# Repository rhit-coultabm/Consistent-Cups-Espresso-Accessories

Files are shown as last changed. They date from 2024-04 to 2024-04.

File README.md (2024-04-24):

# Consistent-Cups-Espresso-Accessories
Open Source DIY solution to create Bluetooth-compatible pressure sensor and scale to use with a manual espresso machine. 

## Table of Contents
- [Consistent-Cups-Espresso-Accessories](#consistent-cups-espresso-accessories)
   - [Table of Contents](#table-of-contents)
   - [Project Background and Introduction](#project-background-and-introduction)
      - [Semi-Automatic Espresso Machines](#semi-automatic-espresso-machines)
      - [Manual Espresso Machines](#manual-espresso-machines)
   - [Description of Solution](#description-of-the-solution)
      - [Bill of Materials](#bill-of-materials)
   - [Pressure Sensor](#pressure-sensor)
      - [Components Used](#components-used)
      - [Casing Files](#casing-files)
      - [Assembly Instructions](#assembly-instructions)
   - [Scale](#scale)
      - [Components Used](#components-used-1)
      - [Casing and PCB Files](#casing-and-pcb-files)
      - [Assembly Instructions](#assembly-instructions-1)
   - [Flashing the Devices](#flashing-the-devices)
   - [Connecting with Profiler Apps](#connecting-with-profiler-apps)

## Project Background and Introduction

The market for espresso machines is a vastly large and competitive one. Every individual has their own preferences and lifestyles which result in the need for different machines. There are so many methods for making espresso that vary significantly in user effort, time, and price. 

### Semi-Automatic Espresso Machines

Automatic machines require little user effort and time to extract an espresso shot. However, the large downside to these machines is that, generally speaking, they cost upwards of $300-400 depending on the additional features and components they have. Once the grinds are tamped in the portafilter, the machine automatically applies the pressure for the duration of time that can sometimes be specified by the user.  

images

Figure 1: Semi-Automatic Espresso Machine Example 

### Manual Espresso Machines

Manual espresso machines require a significant amount of preparation, time, and effort. These machines are generally cheaper than their automatic counterparts, being found for upwards of $100. For these machines, once the grinds are tamped in the portafilter, the user must also heat their water to the desired temperature. The user then needs a scale underneath the cup to be able to see how fast they are extracting the espresso. After pulling the lever and applying pressure for a set amount of time, the extraction is finally complete. The downsides to this machine are the extensive clean-up time and the loss of water temperature during the extraction. However, this machine allows the user to have complete control over the amount of pressure and time variables for making their own ideal cup of espresso, perfect for connoisseurs. With the pressure transducer and scale, it would be even easier to repeat their results or tweak them to their preferences. An example of what this type of machine looks like is in the right image of Figure 3. 

Besides the bean and how it's roasted, a good cup of lever espresso relies on three main factors: Pressure, temperature, and speed of the pull.  The speed of pull is determined by the grind size of the bean and the pressure.  Pressure is controlled by pulling the machine's handle.  A monitor system lets you track and save the pressure and pull speed data to a template.  You can then follow the template when doing a future pull, enabling consistent tasting espresso. 

The downside to such systems is the cost.  An entry-level scale like the Acaia Lunar Espresso Scale is $250, and the pressure gauge is $460 from naked-portafilter (both pictured below). 

Capture

Figure 2: Naked Portafilter Smart Espresso Profiler 

Capture1

Figure 3: Acaia Lunar Espresso Scale 

## Description of the solution

The market for espresso machines is a vastly large and competitive one. Every individual has their own preferences and lifestyles which result in the need for different machines, which vary significantly in user effort, time, and price.  Manual lever espresso machines offer an affordable entrance into brewing quality espresso at home.  A monitor system helps the novice get consistent pulls of espresso by tracking and logging variables like pressure and speed of pull. The existing market design for the pressure sensor is $400 and the scale is $200, a steep cost that ends up at the same price level as some higher-end automatic machines. This solution is an open-source pressure sensor and scale system that wirelessly connects to the SE Profiler or Coffee Flow phone app. This is all accomplishable with the materials posted below in the BOM, a soldering iron, a 3D printer, and a computer!

### Bill of Materials

[BOM.xlsx](https://github.com/rhit-coultabm/Consistent-Cups-Espresso-Accessories/files/15097891/BOM.xlsx)

## Pressure sensor

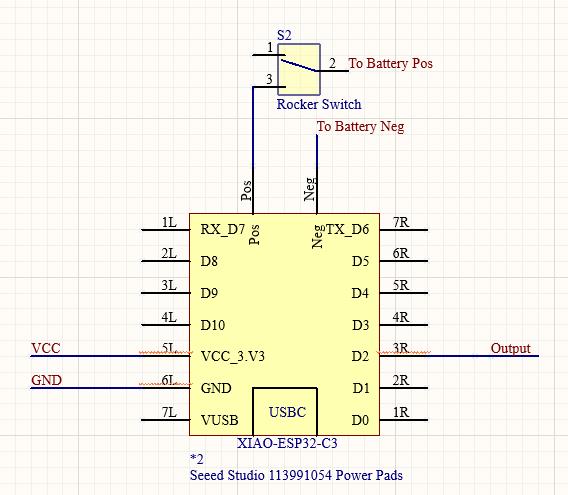
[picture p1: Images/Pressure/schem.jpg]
pressure sensor schematic


Figure 6: Wiring diagram

### Components used
   - Seeduino
   - Pressure Sensor
   - Battery
   - On/off switch
   - Casing
  
   Shown here:
  
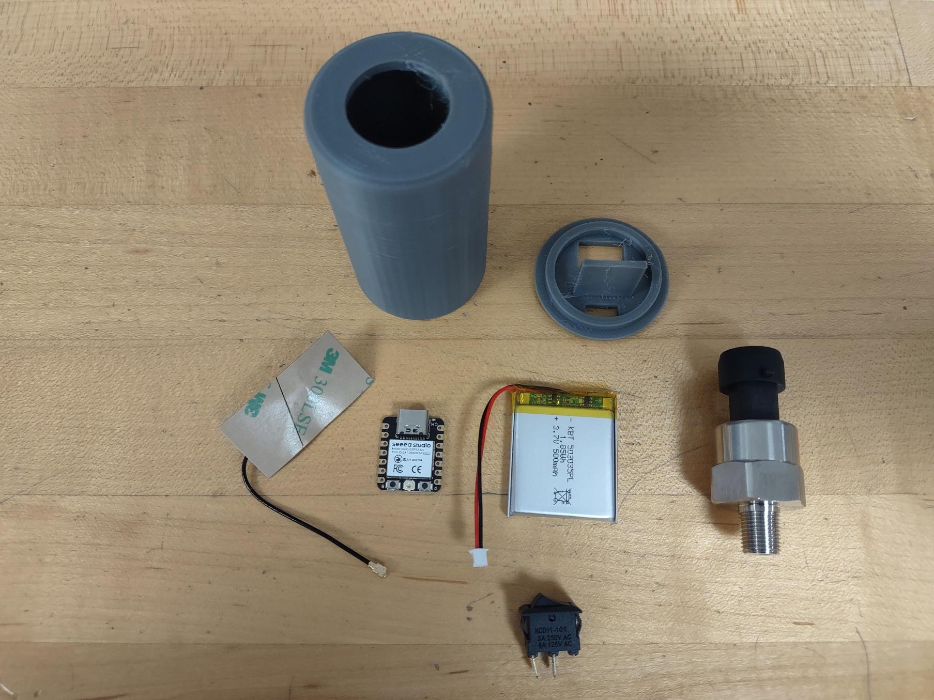
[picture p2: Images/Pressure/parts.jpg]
pressure sensor parts


### Casing files
   
[Body](Enclosure_Files/Pressure_Sensor/pressure_base.STL)

[Cap](Enclosure_Files/Pressure_Sensor/pressure_end.STL)

### Assembly Instructions

#### Step 1: Solder Power connections

- Using the battery, two short wires, and the seeduino (shown below in figure 4) follow the wiring diagram (shown above in figure 6) connecting the battery positive (red) wire to one of the pins on the switch. Then the battery negative (black) wire to the negative pin on the back of the seeduino. Next, solder a wire from the other switch pin to the positive pin on the back of the seeduino. 
- This final product attached to the casing cap is shown below in figure 5

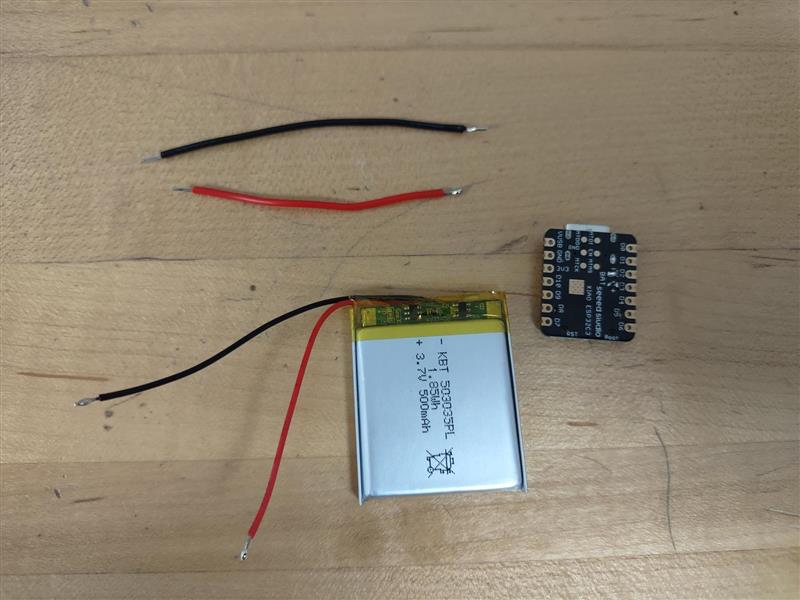
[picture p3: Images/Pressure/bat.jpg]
battery and xiao


Figure 4: Items needed

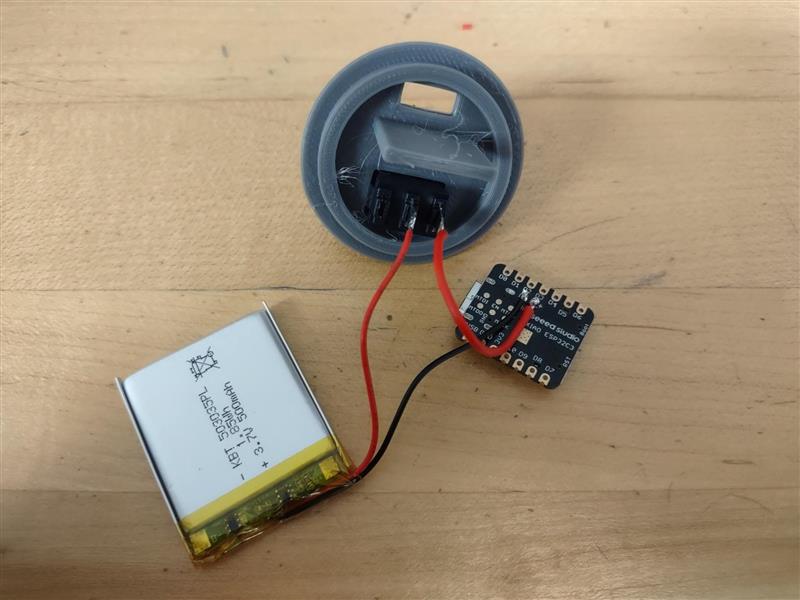
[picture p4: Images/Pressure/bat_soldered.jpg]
battery soldered with switch


Figure 5: final product of this step

#### Step 2: Solder Pressure Sensor

- Using the two figures below, wire the pressure sensor with the Vcc to pin Vcc, the ground to ground, and the output to pin D2
- Make sure that the pressure sensor is wired through the hole in the casing to the seeduino, this is to ensure that it can all be put together in the final step

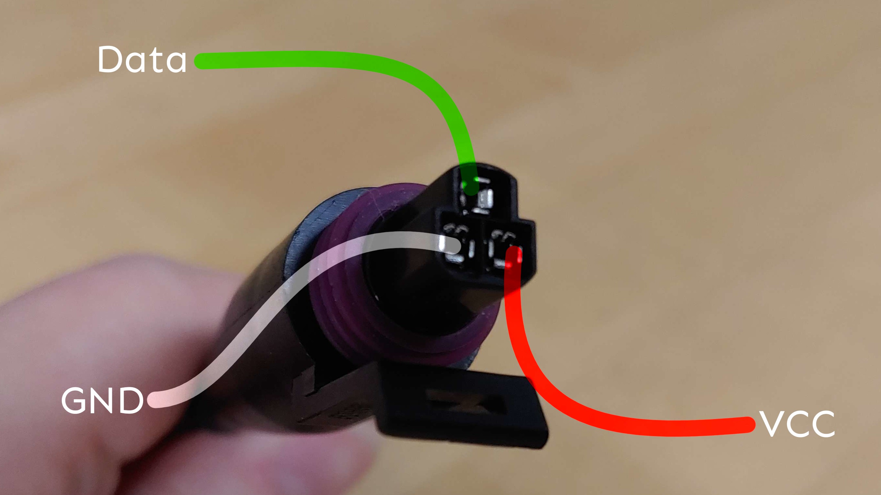
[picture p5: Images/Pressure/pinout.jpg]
sensor pinout


Figure 7: Sensor Wiring assignments

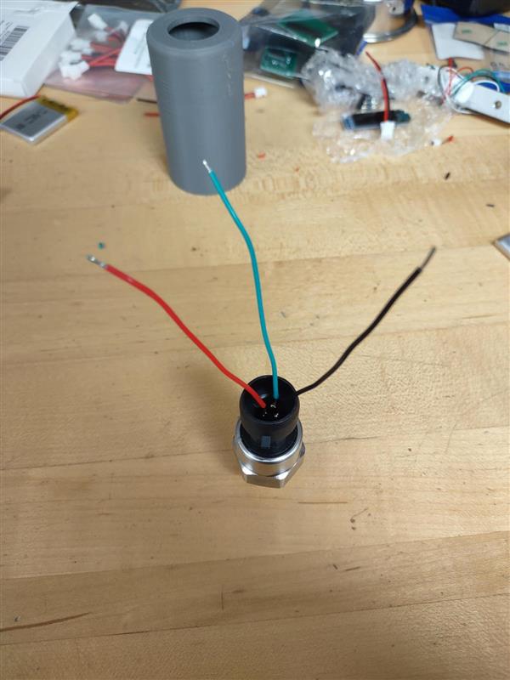
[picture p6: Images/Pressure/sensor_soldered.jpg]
sensor pins soldered


Figure 9: Wired pressure sensors with matching colors from figure 8

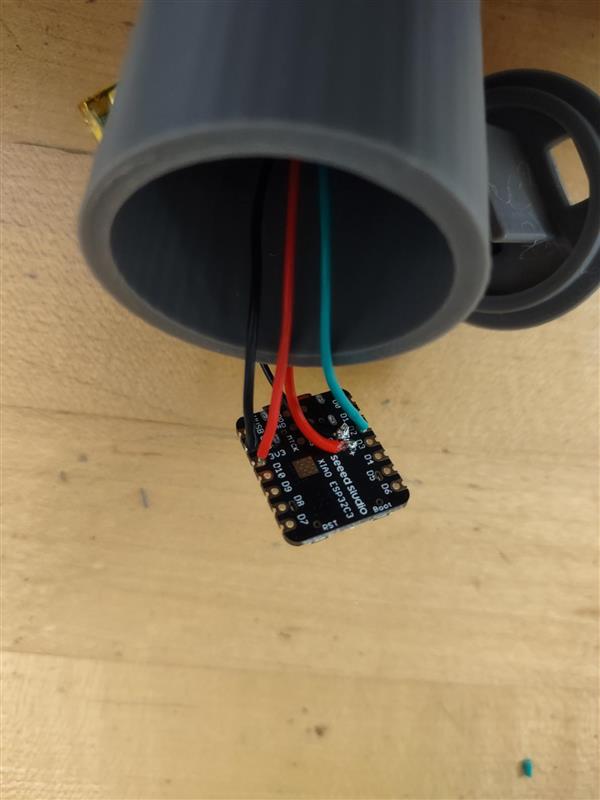
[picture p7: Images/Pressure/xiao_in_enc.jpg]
soldered Seeeduino Xiao in enclosure


Figure 10: Pressure sensor and seeduino attached and put into the casing

#### Step 3: Assemble

- To finalize this part of the pressure sensor, attach the antenna to the seeduino (as shown in figure 11)
- Next, fit all of the components into the casing, with seeduino on the shelf, the battery slotted into the main area of the casing, and the pressure sensor through the hole on the other side of the casing (all shown in figure 12)
- Final product is shown in figure 13 and 14

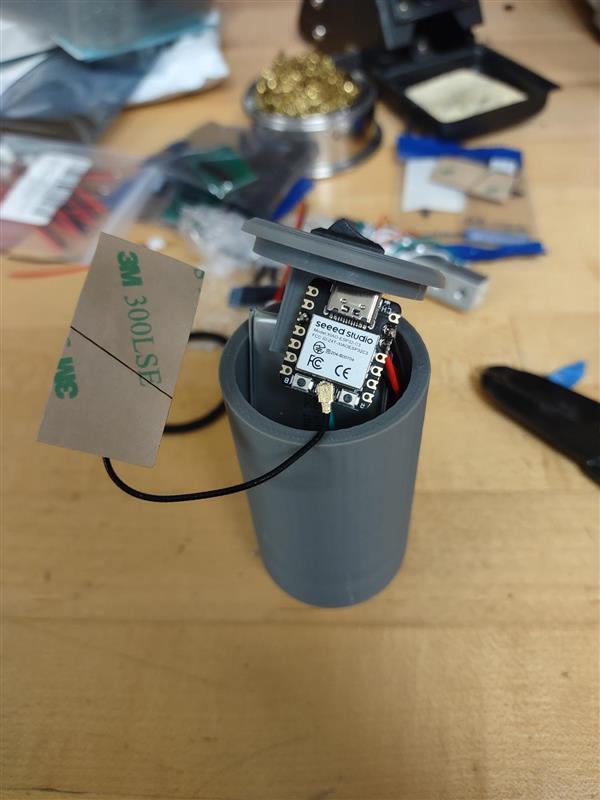
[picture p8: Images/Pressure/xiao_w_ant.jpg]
antenna attachment


Figure 11: Attached antenna to the Seeeduino Xiao

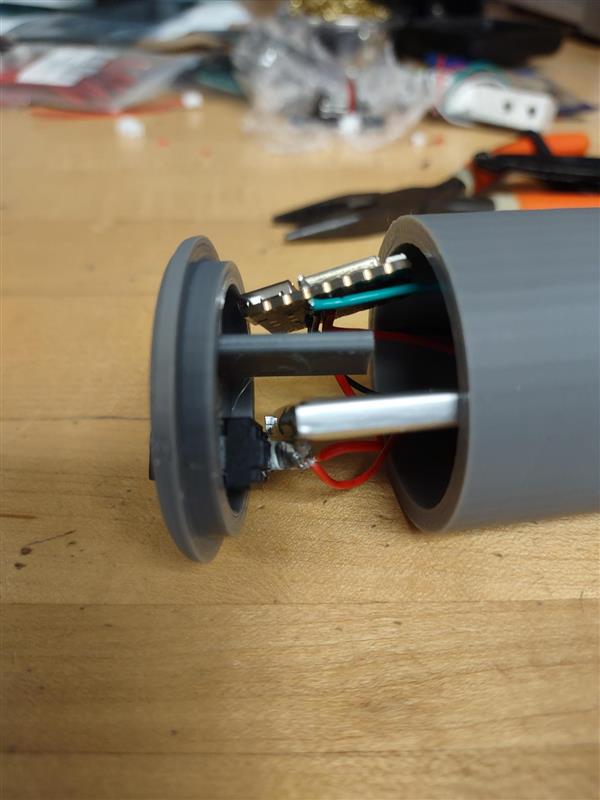
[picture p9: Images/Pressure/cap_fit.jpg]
fitment of components


Figure 12: How to fit the components into the case

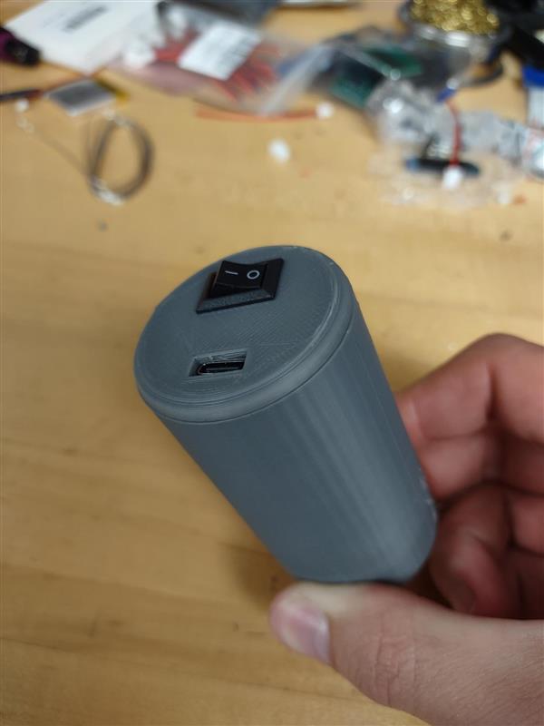
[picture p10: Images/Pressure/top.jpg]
top of assembled sensor


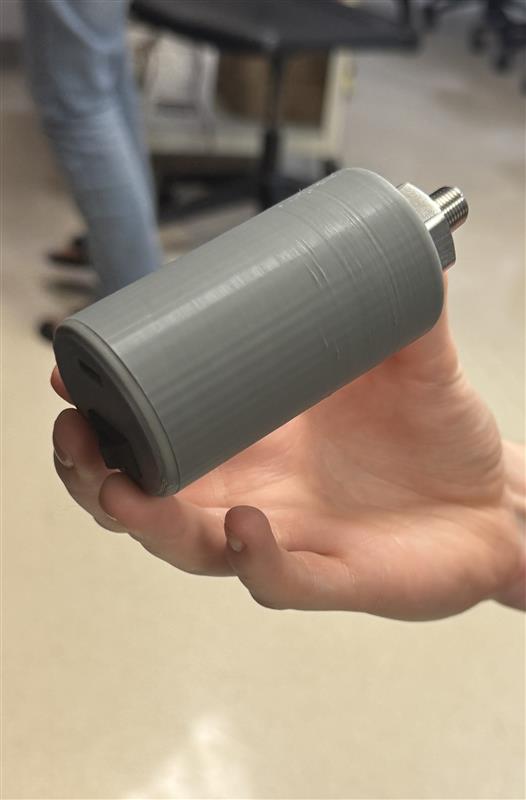
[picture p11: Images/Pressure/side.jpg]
side view of assembled sensor


Figure 13/14: How the casing end should look when all is completed 

## Scale

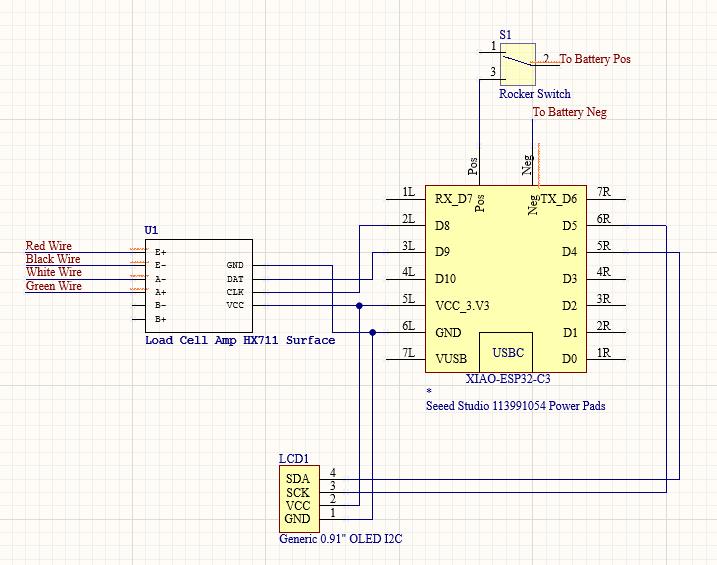
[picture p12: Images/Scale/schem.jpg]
wiring diagram


Figure 16: Wiring diagram 

### Components used
   - Seeduino
   - Load Cell
   - Battery
   - PCB
   - LCD
   - On/off switch
   - Casing
   - Header Pins

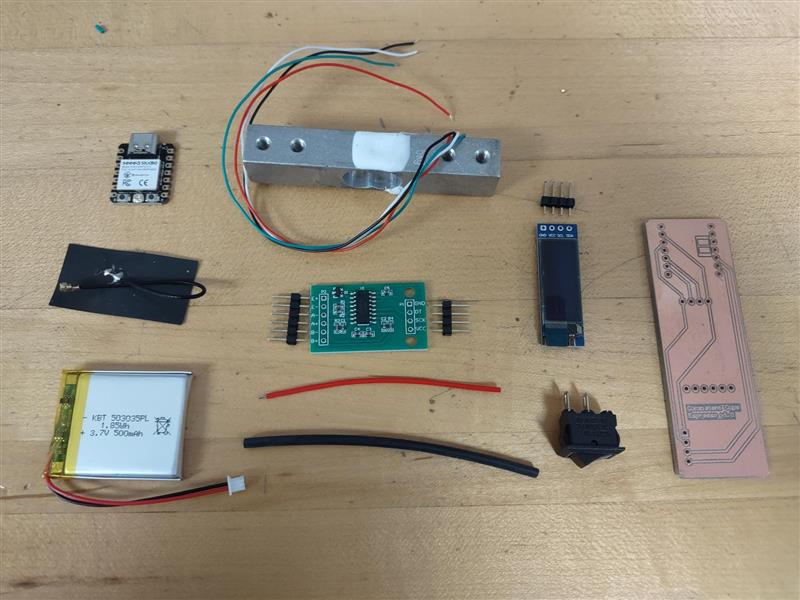
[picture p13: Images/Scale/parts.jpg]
parts required


### Casing and PCB files
   
[Scale Top](Enclosure_Files/Scale/scale_top.STL)

[Scale Bottom](Enclosure_Files/Scale/scale_bottom.STL)

[PCB Files](PCB_Files)

To have a PCB made, you could use [JLPCB](https://jlcpcb.com/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) or similar services. Just select 'Order Now', then upload the Gerber files provided above, select base material as FR-4, and then 'Save to cart' and continue to checkout!

### Assembly Instructions

#### Step 1: Put headers on

- The conponents that are on the BOM still need header pins to properly connect in later steps so use invidiual header pins and add them to the seeduino, the LED screen, and the ADC for the load cell. (all shown below in figure 15) They are added by sticking the short side of the pin through the holes in the bottom side of the component and soldering the top to secure them.  

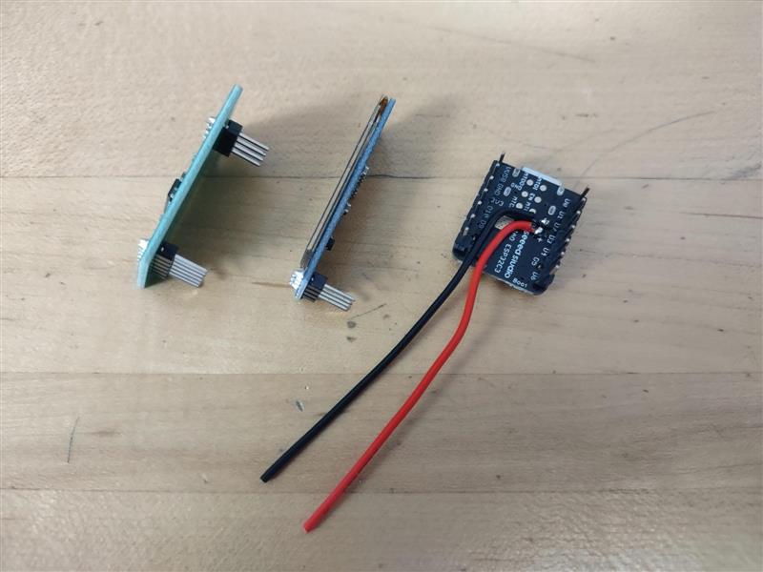
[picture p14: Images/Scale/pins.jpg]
pin attachment


Figure 15: how components look after header pins are attached 

#### Step 2: Solder PCB with components 

- Note that you might have to file the short ends of the PCB down a little to make a snug press fit into the casing. This was done so that any sort of glue was not needed when assembling the system.
- Also note that this PCB is one sided so the components are placed on the side without copper and all of the soldering is done on the side with copper.
  
- Before adding the seeduino to the PCB, solder two small wires to the positive and negative places on the back (shown above in figure 15) this is to add battery connections later 
- The PCB facilitates the the wiring diagram in figure 16
- Follow the PCB layout (figure 17) when placing the components, all pins should have a place if added correctly so if the holes do not line up the components are in the incorrect place.

- To wire the load cell, position the PCB with the compoennts facing down and the LED screen on the bottom. Next, following Figure 18, connect the wires in this order from left to right: green, white, black, and red.

- In our solution we applied a heat shrink wrap around the load cell connections so ensure that when placed into the case the connections are still strong. This is not a required step so it is not included in the BOM but an alternative would be to wrap electrical wire around the connections and it will functions the same as the heat shrink wrap. 

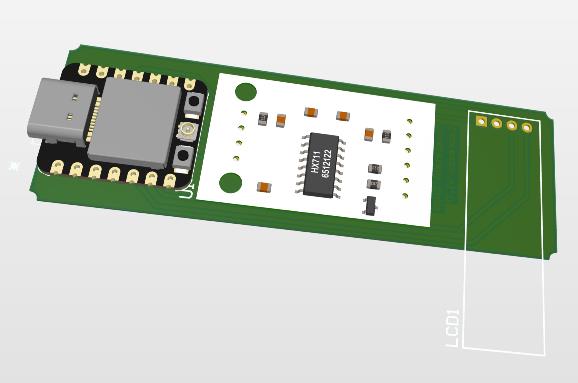
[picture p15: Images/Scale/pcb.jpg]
CAD model of PCB


Figure 17: Digital PCB layout

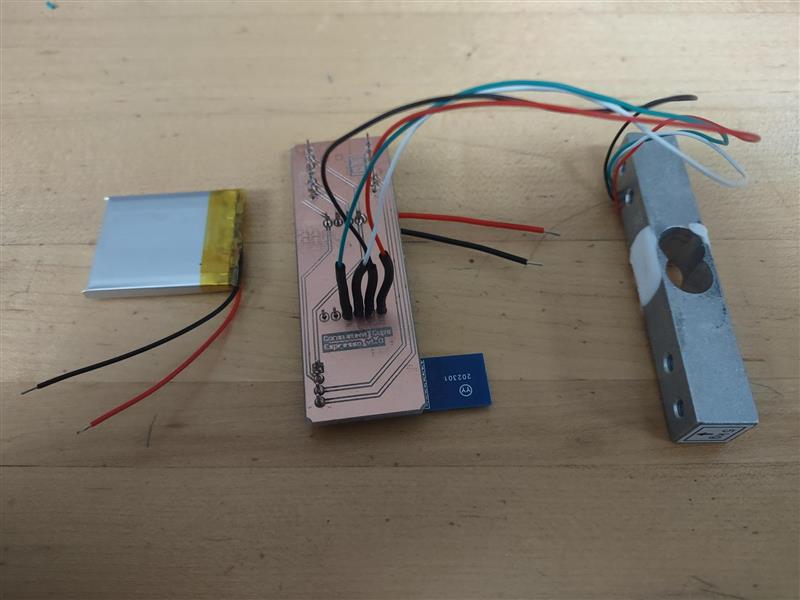
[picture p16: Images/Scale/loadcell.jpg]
Loadcell soldered to PCB


Figure 18: soldered load cell

#### Step 3: Add battery connections

- Continuing to follow the wiring diagram from above
- It is probably easiest if you place the switch in the small rectangular hole on the side of the top part of the scale casing before continuting, then soldering with the switch in place 
- Connect a wire from the positive pin of the seeduino and one side of the switch. Then connect the positive side of the battery to the other pin on the switch and the negative side of the battery to the negative pin on the seeduino.

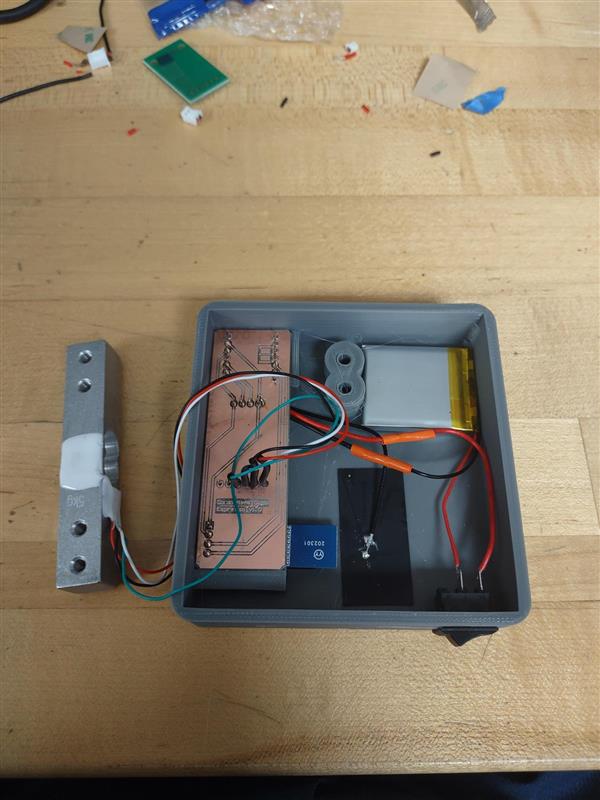
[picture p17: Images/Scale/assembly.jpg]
Placing components in scale enclosure top


Figure 19: Fully soldered components placed into the casing

#### Step 4: Assemble 

- When placing the PCB into the casing it is important to flip it upside down. The side with the components should be facing down into the casing. The seeduino port should stick out of the indentation and the side of the casing.
- Next, the battery can be placed loose on the side of the casing with the switch, it can also be hot glued down but this inhibits quick battery changes in the future if needed
- Now the load cell needs to be added
     - On the side of the load cell there is a sticker with and arrow and this arrow should be facing opposite the inside of the casing. So if the casing is positioned like in Figure 20, then the arrow will be facing the ceiling.
     - Next, holding the load cell in place, flip the casing over and attach the screws to the two holes on the top.
- Finally, attach the bottom (thinner) part of the casing to the other side of the load cell with two more screws

- As a last step, we added a small piece of acrylic to the LED screen hole on the top of the casing with hot glue or other adhesive. Be careful with superglue which may cause the acrylic to appear cloudy as the adhesive dries. This is to help waterproof the system so that none of the components are damaged if water or coffee gets into the system. 

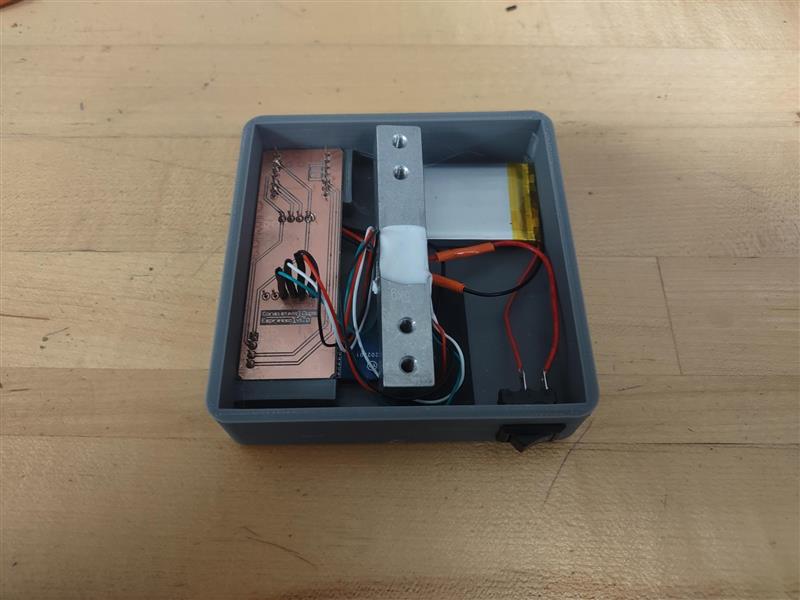
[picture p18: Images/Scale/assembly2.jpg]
Assembled scale top


Figure 20: Fully assembled top of enclosure

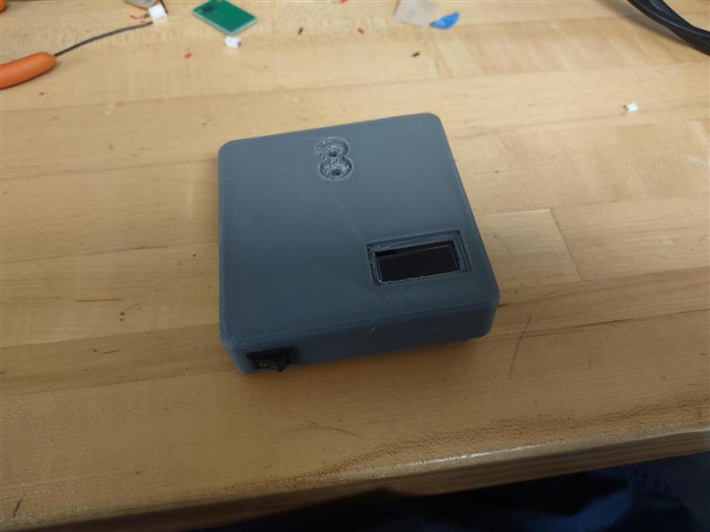
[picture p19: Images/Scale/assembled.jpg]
final scale


Figure 21: Fully assembled scale

## Flashing the Devices

The firmware code for each respective device can be found under the [Arduino folder](Arduino) of this repository.

In order to flash the firmware to the devices, the Arduino files must be opened in an [Arduino IDE](https://www.arduino.cc/en/software) set up for ESP32. We used the Legacy IDE (1.8.X) in the development process.

### ESP32 + Arduino

We recommend following the [instructions provided by Espressif](https://docs.espressif.com/projects/arduino-esp32/en/latest/installing.html) for setting up the ability to compile for and flash to ESP32. Once complete, click on tools, hover over the board, and scroll until you find "XIAO_ESP32C3" then select that as your target board.

With the port the device is connected to via USB selected, click the upload button and wait for the compiling and flashing process to complete.

## Connecting with Profiler Apps

The apps used to interface with this system are called SE Profiler and Pressensor CF. Both of which are available on Apple and Android smartphones. 

The first step in using your system is to charge the batteries. To do this: 
- Plug a type c connecter into the seeduino port and then into the wall or a computer. This should be all that is needed to charge the system. The seeduino has automatic charging hardware that will charge the system without any added components. Charging the batteries for around 30 min to 1 hour time will be fully charged and should last for around 1 week time.

The next step in using your system is to flash the seeduinos with the Arduino code provided. To do this : 

After the code is flashed, connect both seeduinos to your phone via Bluetooth. Open the application of choice (in this we will show SE profiler). 

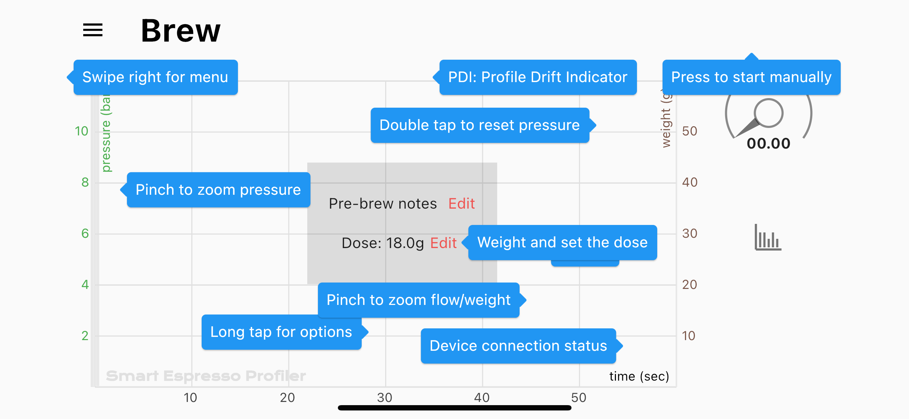
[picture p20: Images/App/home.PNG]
Home screen


Figure 22: Home screen of SE profiler app

Navigate to the "Devices" page using the sidebar menu, it looks like the following.

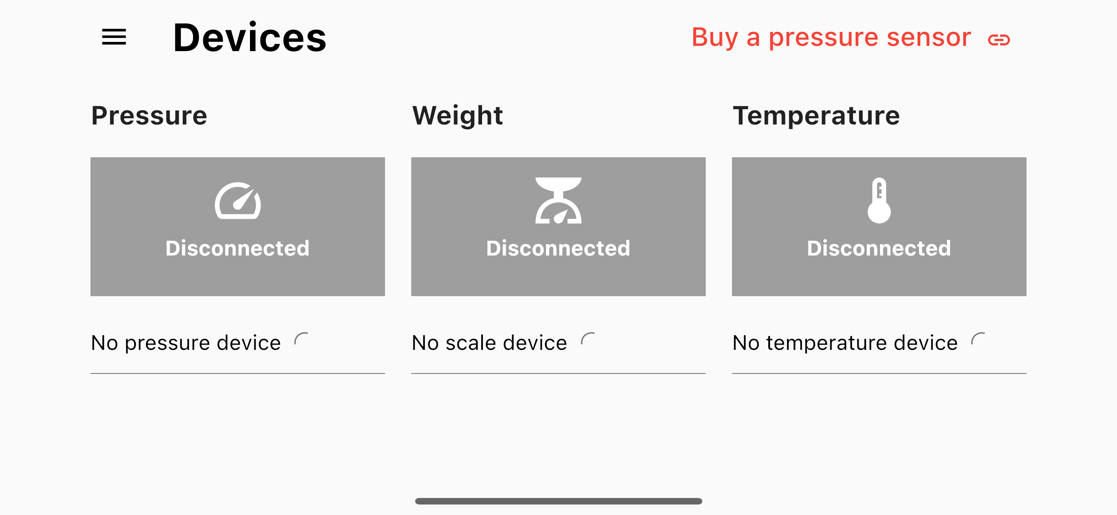
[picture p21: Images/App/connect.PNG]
Devices page


Figure 23: Devices page of SE profiler app

On this page, connect to the scale and pressure sensor, temperature will not be used here. Once both are connected, go back to the home screen. Change the dosage to the desired weight for the amount of espresso being used. 

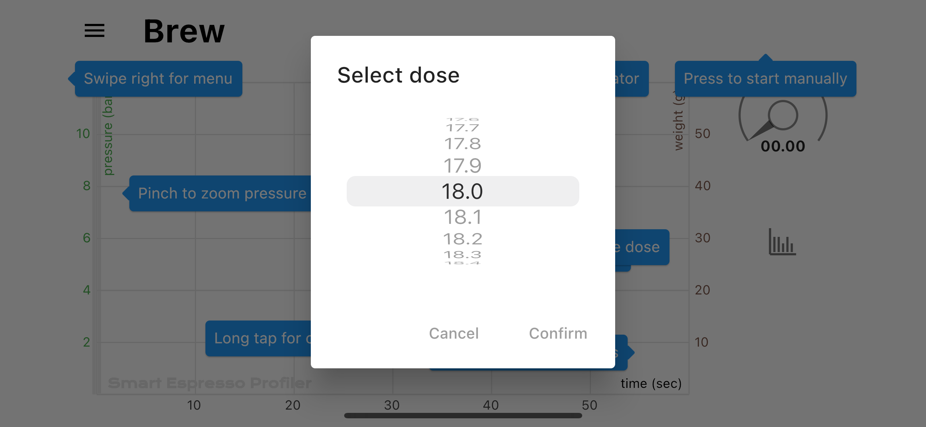
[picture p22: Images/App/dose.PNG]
Dose size


Figure 24: Page used to select espresso grind dosage.

Once the grind is set, tare the scale in the app after setting up the cup and the rest of the system. A start button should appear in the top right corner and this can be selected to begin the sensor measurements and process. Click stop once the shot has been pulled, if the current graph is desirable it can be saved into history to be used as a reference at a later date.

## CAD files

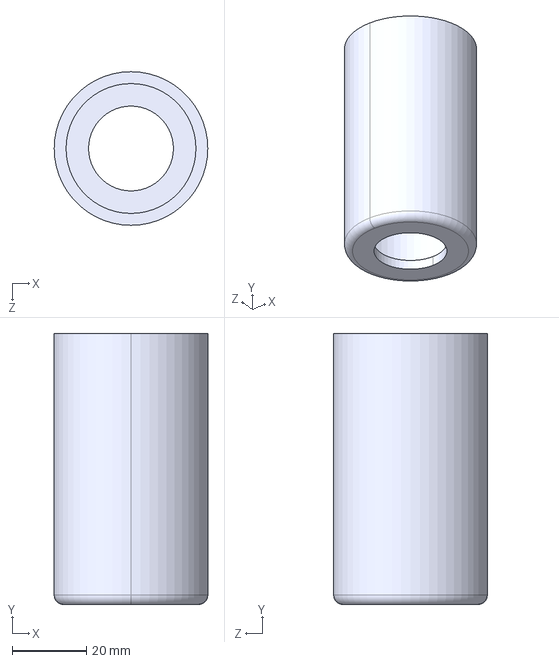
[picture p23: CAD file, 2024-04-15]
Enclosure_Files/Pressure_Sensor/pressure_base.STEP
41.4 x 73.0 x 41.4 mm

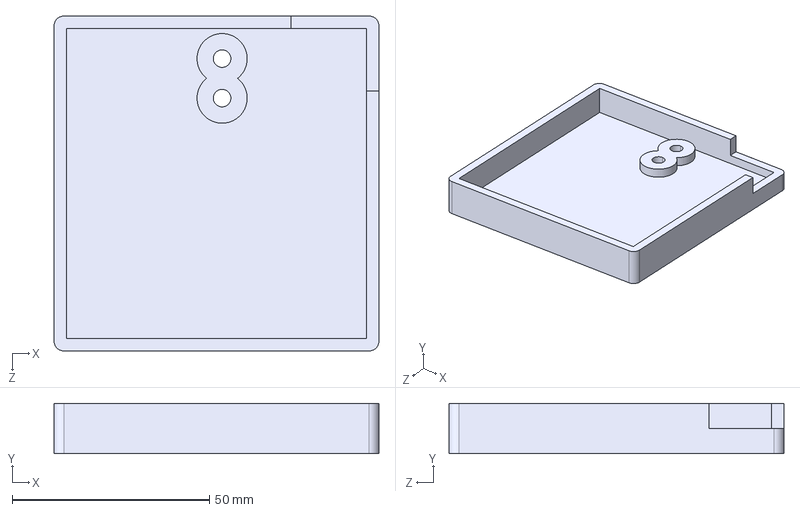
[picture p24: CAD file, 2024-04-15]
Enclosure_Files/Scale/scale_bottom.STEP
82.3 x 12.7 x 84.8 mm

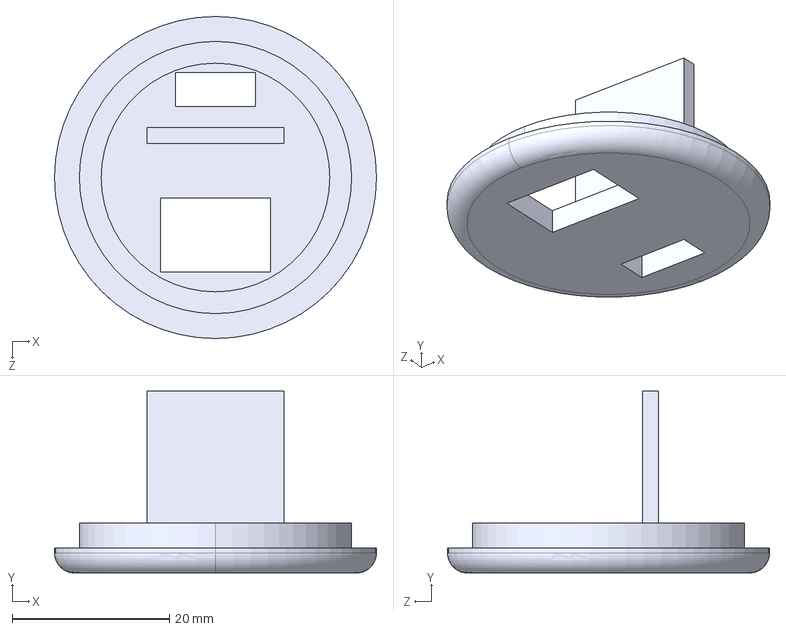
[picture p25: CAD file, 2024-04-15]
Enclosure_Files/Pressure_Sensor/pressure_end.STEP
41.0 x 23.2 x 41.0 mm

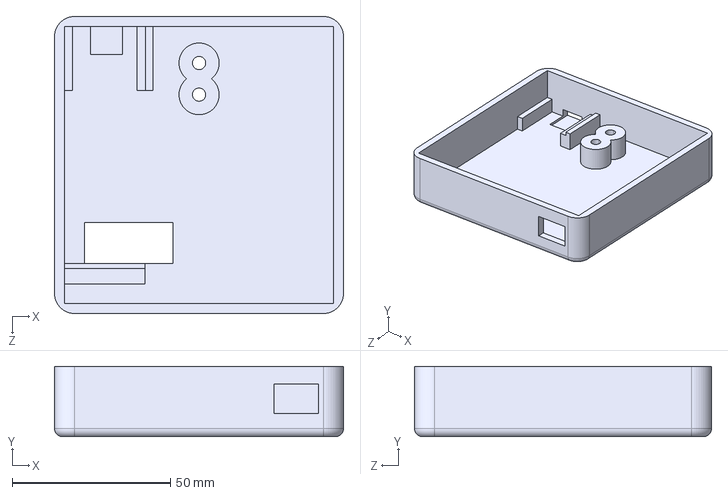
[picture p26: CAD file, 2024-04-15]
Enclosure_Files/Scale/scale_top.STEP
91.4 x 22.2 x 94.0 mm

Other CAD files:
Enclosure_Files/Pressure_Sensor/pressure_base.STL
Enclosure_Files/Pressure_Sensor/pressure_end.STL
Enclosure_Files/Scale/scale_bottom.STL
Enclosure_Files/Scale/scale_top.STL

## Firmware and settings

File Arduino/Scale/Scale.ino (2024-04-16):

/*
  Written by Bryce Bejlovec following the BLE example code
  by Neil Kolban and Evandro Copercini

  Implementation of scale firmware based on Decent Scale v1.2 functionality
*/
#include <BLEDevice.h>
#include <BLEServer.h>
#include <BLEUtils.h>
#include <BLE2902.h>
#include "HX711.h"
#include <SPI.h>
#include <Wire.h>

// OLED Display
#include <Adafruit_GFX.h>
#include <Adafruit_SSD1306.h>
#define SCREEN_WIDTH 128 // OLED display width, in pixels
#define SCREEN_HEIGHT 32 // OLED display height, in pixels
#define OLED_RESET     -1 // Reset pin # (or -1 if sharing Arduino reset pin)
#define SCREEN_ADDRESS 0x3C ///< See datasheet for Address; 0x3D for 128x64, 0x3C for 128x32
Adafruit_SSD1306 display(SCREEN_WIDTH, SCREEN_HEIGHT, &Wire, OLED_RESET);


//HX711
const int LOADCELL_DOUT_PIN = 9;
const int LOADCELL_SCK_PIN  = 8;
float zero = 0;
float cal = 22.4*0.829;//44.8525;11.213125;
float curread = 0;
float oldread = 0;
float old2read = 0;
float curvalue = 0;
float oldval = 0;
HX711 scale;

// Bluetooth
BLEServer* scaleServer = NULL;
BLECharacteristic* weightCharacteristic = NULL;
BLECharacteristic* rCharacteristic = NULL;
bool deviceConnected = false;
bool newDiscon = true;
// Packet
uint8_t value[10] = {0x03, 0xCA, 0, 0, 0, 0, 0, 0, 0, 0};
int16_t *weight = (int16_t*)&value[2];
int8_t *minutes = (int8_t*)&value[4];
int8_t *seconds = (int8_t*)&value[5];
int8_t *milsecs = (int8_t*)&value[6];

// Variables
//int16_t zero = 0;
int16_t tareValue = 0;
int16_t curW = 0;
int16_t oldW = 0;
uint32_t timer = 0;
uint32_t curT = 0;
uint8_t  timeControl = 0;

#define SCALE_SERVICE_UUID            "0000FFF0-0000-1000-8000-00805F9B34FB" //"9B38F367-5546-A4E1-4DA5-0661A0F71267"
#define WEIGHT_CHARACTERISTIC_UUID    "0000FFF4-0000-1000-8000-00805F9B34FB"
#define RECEIVE_CHARACTERISTIC_UUID   "000036F5-0000-1000-8000-00805F9B34FB"


class scaleServerCallbacks: public BLEServerCallbacks {
    void onConnect(BLEServer* scaleServer) {
      deviceConnected = true;
    };

    void onDisconnect(BLEServer* scaleServer) {
      deviceConnected = false;
      delay(500); // give the bluetooth stack the chance to get things ready
      scaleServer->startAdvertising(); // restart advertising
//      Serial.println("start advertising");
      timer = millis();
    }
};

// Used to receive commands from the profiling app.
class ReceiveCallbacks: public BLECharacteristicCallbacks {
    void onWrite(BLECharacteristic *rCharacteristic) {
      std::string packet = rCharacteristic->getValue();
      switch ((uint8_t)packet[1]) {
        case 0x0A:
          if ((uint8_t)packet[2]) {
            //LED On Maybe turn on the screen? Unused feature
          } else
            // LED Off Maybe turn off the screen? Unused feature
            break;
        case 0x0B:
          switch ((uint8_t)packet[2]) {
            case 0x00:
              //Timer stop
              timeControl = 32;
              break;
            case 0x03:
              //Timer Start
              timeControl = 0;
              timer = millis();
              break;
          }
          break;
        case 0x0F:
          zero = scale.read_average(10);
          break;
        default:
          break;
      }
    }
};

void BLEinit() {
  // create the BLE device
  BLEDevice::init("Decent Scale");

  // Create the server
  scaleServer = BLEDevice::createServer();
  scaleServer->setCallbacks(new scaleServerCallbacks());

  // Create the BLE Service
  BLEService *scaleService = scaleServer->createService(SCALE_SERVICE_UUID);

  // Instanciate characteristics and properties
  weightCharacteristic = scaleService->createCharacteristic(
                           WEIGHT_CHARACTERISTIC_UUID,
                           BLECharacteristic::PROPERTY_READ |
                           BLECharacteristic::PROPERTY_NOTIFY);
  rCharacteristic = scaleService->createCharacteristic(
                      RECEIVE_CHARACTERISTIC_UUID,
                      BLECharacteristic::PROPERTY_READ  |
                      BLECharacteristic::PROPERTY_WRITE);
  // Add callbacks for packets received
  rCharacteristic->setCallbacks(new ReceiveCallbacks());
  weightCharacteristic->addDescriptor(new BLE2902());
  // Start the service
  scaleService->start();
}

void advertiseBLE() {

  // Start advertising
  BLEAdvertising *scaleAdvertising = BLEDevice::getAdvertising();
  scaleAdvertising->addServiceUUID(SCALE_SERVICE_UUID);
  scaleAdvertising->setScanResponse(false);
  scaleAdvertising->setMinPreferred(0x0);  // set value to 0x00 to not advertise this parameter
  BLEDevice::startAdvertising();
}

void initScale() {
  scale.begin(LOADCELL_DOUT_PIN, LOADCELL_SCK_PIN);
  scale.power_up();
  scale.set_gain(64);
  display.print("Calibrating");
  delay(1000);
  zero = scale.read_average(10);
  // Zero Loop
  while(abs(scale.read()-zero) < 10){
    zero = scale.read_average(3);
    delay(100);
  }
}

void initOLED() {
  if (!display.begin(SSD1306_SWITCHCAPVCC, SCREEN_ADDRESS)) {
     
  }
  // init OLED screen
  display.clearDisplay();
  display.setTextSize(2);             // Normal 1:1 pixel scale
  display.setTextColor(SSD1306_WHITE);        // Draw white text
  display.setCursor(0, 0);            // Start at top-left corner
  display.setRotation(2);
}

void setup() { 
  BLEinit();
  initOLED();
  
  timer = millis();
  
  initScale();
  advertiseBLE();
  
  curread = scale.read();
  curW = (uint16_t)((curread - zero) / cal);
  delay(500); // give the bluetooth stack the chance to get things ready
  scaleServer->startAdvertising(); // restart advertising
}

void scaleLoop(){
  display.clearDisplay();
  oldW = curW;
  if (scale.is_ready()) {
    old2read = oldread;
    oldread = curread;
    curread = scale.read();
    oldval = curvalue;
    
    // Filter direct reading
    if (abs(oldread - curread) >= 15 && old2read - curread < 200) {
      curvalue = (2 * curread + 3 * old2read + 3 * oldread) / 8;
      curread = (curread + oldread + old2read) / 3;
    } else {
      curvalue = (5 * curread + old2read + 2 * oldread) / 8;
    }

    // Filter tared and calibrated value
    curW = (uint16_t)((curvalue - zero) / cal);
    if (abs(oldW - curW) < 2) {
      curW = (5 * oldW + 3 * curW) >> 3;
    } else {
      curW = (3 * oldW + 5 * curW) >> 3;
    }

    // Display
    display.clearDisplay();
    display.setCursor(0, 0);
    display.print(curW/10.0);
    display.print("g");
    display.display();
  }
  else {
    curW = curW;
  }
}

void loop() {
  scaleLoop();
  // notify changed value
  if (deviceConnected) {
    if (curW != oldW)
      value[1] = 0xCA; // Changing
    else
      value[1] = 0xCE; // Stable

    curT = (millis() - timer) >> (uint32_t)timeControl; // Find current running time or

    // Set timestamp in packet
    *minutes = (uint8_t)(curT / 60000);
    *seconds = (uint8_t)((curT % 60000) / 1000);
    *milsecs = (uint8_t)((curT % 1000) / 100);

    // Set weight in packet to tared weight
    *weight = curW; // - tareValue;
    *weight = (*weight << 8) | (*weight >> 8); // Convert Little-Endian to Big-Endian, RISC-V is little-endian

    // XOR packet for checksum
    value[9] = value[0] ^ value[1] ^ value[2] ^ value[3] ^ value[4] ^ value[5] ^ value[6] ^ value[7] ^ value[8];

    // Send packet
    weightCharacteristic->setValue((uint8_t*)value, 10);
    weightCharacteristic->notify();
    delay(95); // 100ms delay for 10Hz packets, putting 95 for now
  } else {
    if (millis() - timer >= 300000) {
      // Sleep when timed out
      scale.power_down();
      display.clearDisplay();
      esp_deep_sleep_enable_gpio_wakeup(BIT(D2), ESP_GPIO_WAKEUP_GPIO_HIGH);
      esp_deep_sleep_start();
    }
  }
}

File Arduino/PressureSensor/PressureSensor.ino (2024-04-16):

/*
  Written by Bryce Bejlovec following the BLE example code
  by Neil Kolban and Evandro Copercini

  Implementation of pressure transducer firmware based on PRS
*/
#include <BLEDevice.h>
#include <BLEServer.h>
#include <BLEUtils.h>
#include <BLE2902.h>

BLEServer* pServer = NULL;
BLECharacteristic* pCharacteristic = NULL;
BLECharacteristic* zCharacteristic = NULL;
bool deviceConnected = false;
bool oldDeviceConnected = false;
int16_t value = 0;
int16_t zero = 0;
uint32_t disconnected = 0;

// Characteristics defined by PRS (https://pressensor.com/pages/prs-protocol)
#define PRESSURE_SERVICE_UUID        "873ae82a-4c5a-4342-b539-9d900bf7ebd0"
#define PRESSURE_CHARACTERISTIC_UUID "873ae82b-4c5a-4342-b539-9d900bf7ebd0"
#define ZERO_CHARACTERISTIC_UUID     "873ae82c-4c5a-4342-b539-9d900bf7ebd0"


class ServerCallbacks: public BLEServerCallbacks {
    void onConnect(BLEServer* pServer) {
      deviceConnected = true;
    };

    void onDisconnect(BLEServer* pServer) {
      deviceConnected = false;
      delay(500); // give the bluetooth stack the chance to get things ready
      pServer->startAdvertising(); // restart advertising
      Serial.println("start advertising");
      oldDeviceConnected = deviceConnected;
      zCharacteristic->setValue((uint8_t*)&zero, 2);
      pCharacteristic->setValue((uint8_t*)&zero, 2);
    }
};

// Used to set the zero value in the profiling app.
class ZeroCallbacks: public BLECharacteristicCallbacks {
    void onRead(BLECharacteristic *zCharacteristic) {
      zCharacteristic->setValue((uint8_t*)&zero, 2);
      pCharacteristic->setValue((uint8_t*)&zero, 2);
    }
};


void setup() {
//  Serial.begin(115200); // DEBUG

  // Create the BLE Device, name required for in-app detection
  BLEDevice::init("PRS");

  // Create the BLE Server
  pServer = BLEDevice::createServer();
  pServer->setCallbacks(new ServerCallbacks());

  // Create the BLE Service
  BLEService *pService = pServer->createService(PRESSURE_SERVICE_UUID);

  // Create a BLE Characteristic
  pCharacteristic = pService->createCharacteristic(
                      PRESSURE_CHARACTERISTIC_UUID,
                      BLECharacteristic::PROPERTY_WRITE  |
                      BLECharacteristic::PROPERTY_NOTIFY 
                    );
  zCharacteristic = pService->createCharacteristic(
                      ZERO_CHARACTERISTIC_UUID,
                      BLECharacteristic::PROPERTY_READ  |
                      BLECharacteristic::PROPERTY_WRITE 
                    );
  zCharacteristic->setCallbacks(new ZeroCallbacks());

  // Create a BLE Descriptor
  pCharacteristic->addDescriptor(new BLE2902());

  // Set initial value to zero so that the app can be calibrated properly. 
  zCharacteristic->setValue((uint8_t*)&zero, 2);
  pCharacteristic->setValue((uint8_t*)&zero, 2);
  analogReadResolution(12); // 12 Bit read resolution to maximize precision when reading the pressure sensor.
  disconnected = millis();
  // Start the service
  pService->start();

  // Start advertising
  BLEAdvertising *pAdvertising = BLEDevice::getAdvertising();
  pAdvertising->addServiceUUID(PRESSURE_SERVICE_UUID);
  pAdvertising->setScanResponse(false);
  pAdvertising->setMinPreferred(0x0);  // set value to 0x00 to not advertise this parameter
  BLEDevice::startAdvertising();
//  Serial.println("Waiting a client connection to notify..."); // DEBUG
}

void loop() {
    // notify changed value
    if(deviceConnected){
      while (deviceConnected) {
        value = analogReadMilliVolts(A2);
        // Convert ADC output to millibar, 0 PSI default to 340, divide by 0.2 to scale to millibar
        value = (int16_t)((float)(value-340)/0.2);
        value = (value<<8)|(value>>8); // Convert Little-Endian to Big-Endian, RISC-V is little-endian
        pCharacteristic->setValue((uint8_t*)&value, 2);
        pCharacteristic->notify();
        delay(20);
      }
      disconnected = millis();
    } else if(millis()-disconnected >= 60000){
        // Wake on active-high signal on pin 2
        esp_deep_sleep_enable_gpio_wakeup(BIT(D2), ESP_GPIO_WAKEUP_GPIO_HIGH);
        esp_deep_sleep_start();
    }
}

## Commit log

2024-04-02 Added initial push of Arduino code
2024-04-15 Enclosure files added .STL and .STEP
    [pressure_base.STEP, pressure_base.STL, pressure_end.STEP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]
2024-04-15 Update README.md
    pressure sensor step 1
2024-04-15 Update README.md
    step 2 pressure sensor
2024-04-15 Update README.md
    pressure sensor pictures added
2024-04-15 Added PCB Files folder
    [PCB1.GBL, PCB1.GKO]
2024-04-16 Added Arduino instructions
2024-04-16 Changed ESP32 Arduino instruction link
